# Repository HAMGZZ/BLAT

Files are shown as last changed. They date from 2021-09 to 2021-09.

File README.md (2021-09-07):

# BLAT!
BLAT! is a board that controls the OEM BiModel on the holden commodore SSV series. Initially made to retrofit them to an older 2010 commodore. BLAT! can interface with the [SoundBoi](https://github.com/HAMGZZ/SoundBoi) controller that connects to the car and automatically controls the valves.

## Exhaust Valve Pinout:
1. GND
2. SIGNAL
3. NC
4. +12V
5. NC(May not be present)

## Electronic signal specification
The signal going to the valve must be a 200Hz PWM signal at 10V (0-10V). At 20% duty cycle the valve will be closed and at 80% duty cycle the valve will be open.

BLAT! Converts simple 0-5V logic signal into the required 10v PWM 200Hz signal. Further this board controls the power to the valves through the relay.

## PCB:
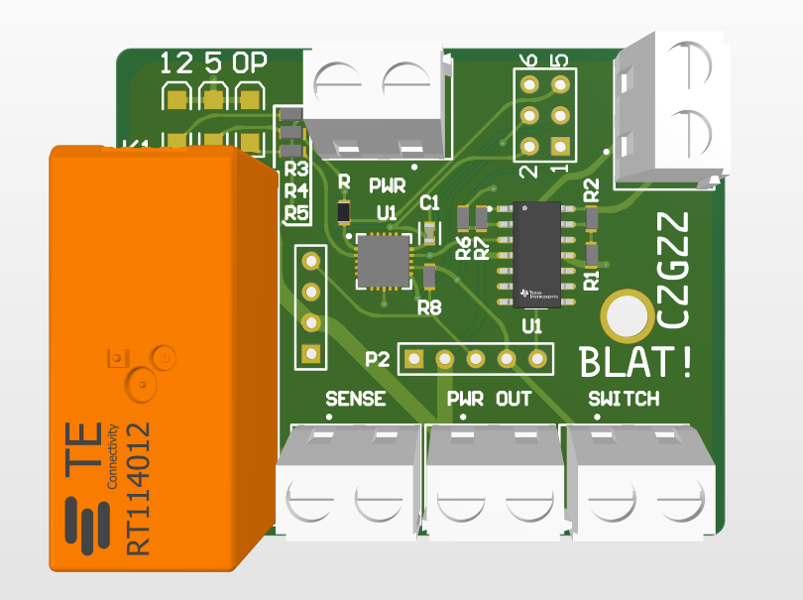
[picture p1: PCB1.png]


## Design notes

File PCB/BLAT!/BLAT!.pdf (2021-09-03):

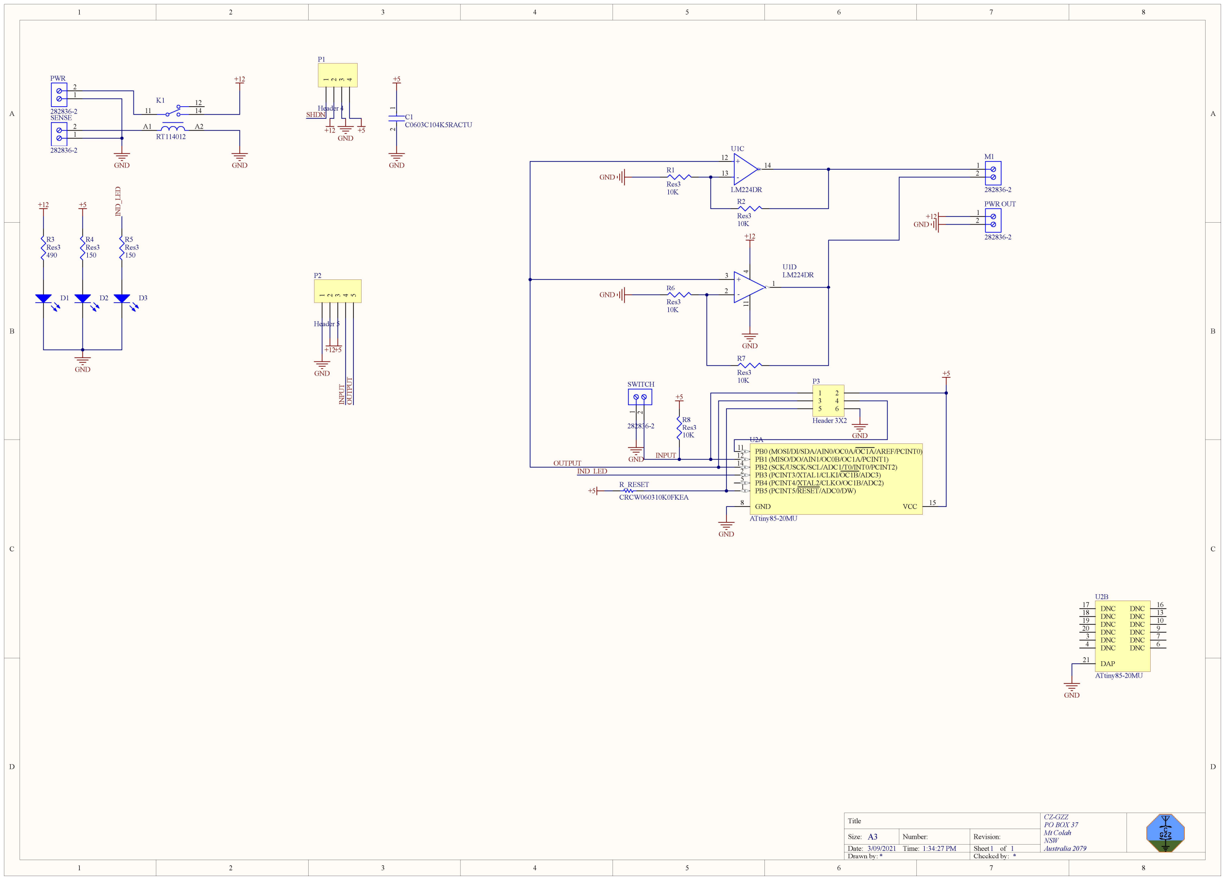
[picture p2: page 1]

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
CZ-GZZ
PO BOX 37
Mt Colah
NSW
3/09/2021 | 1:34:27 PM | 1 | Australia 2079
*

Title

Size: | Number:
Date:
Drawn by:

Revision:
Time: | Sheet | of

A3

Checked by: *

R_RESET
CRCW060310K0FKEA

1 2
C1
C0603C104K5RACTU

GND

GND

GND

1 2
3 4
5 6

P3

Header 3X2

PB5 (PCINT5/RESET/ADC0/DW) 1

PB3 (PCINT3/XTAL1/CLKI/OC1B/ADC3) 2
PB4 (PCINT4/XTAL2/CLKO/OC1B/ADC2) 5

GND 8

PB0 (MOSI/DI/SDA/AIN0/OC0A/OC1A/AREF/PCINT0) 11 PB1 (MISO/DO/AIN1/OC0B/OC1A/PCINT1) 12
PB2 (SCK/USCK/SCL/ADC1/T0/INT0/PCINT2) 14

VCC 15

U2A

ATtiny85-20MU

DNC 17
DNC 18
DNC 19
DNC 20
DNC 3
DNC 4 | DNC | 6
| DNC | 7
DNC | 9
DNC | 10 DNC | 13 DNC | 16

DAP 21

U2B

ATtiny85-20MU

GND

12

13

14 +

U1C

LM224DR

+

3

2

### 1 ⁴ 11

U1D
LM224DR
A1 | A2
| 12
11 14

K1

RT114012

GND

1

2

SENSE

282836-2

1

2

PWR

282836-2

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
Header 4

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
282836-2

10K

R7
Res3

10K

R6
Res3

10K

R2
Res3

10K

R1
Res3

GND

GND

1
2

PWR OUT

282836-2

+12
GND

1
2

SWITCH

282836-2
10K

R8
Res3

+5

GND

D1 | D2 | D3

150

R5
Res3
150

R4
Res3
490

R3
Res3
+12 | +5 | IND_LED

IND_LED

GND | 1
| 2

3

4

5

P2

Header 5

GND

+12+5

+5

INPUT

OUTPUT INPUT OUTPUT

SHDN

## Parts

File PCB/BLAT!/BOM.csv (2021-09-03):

MPN | QTY | PKG | VALUE | COMMENT | DESIGNATOR
LM224DR2G | 1 | SOIC14 |  | 4x OPAMP LM224 | U1
RT114012 | 1 | TH | 12A 12V | 12V Relay | K1
282836-2 | 5 | TH |  | Terminal Block | **
ATTINY85-20MU | 1 | QFN |  | Atmel AVR Microcontroller | U2
RC0603FR-07470RL | 1 | 603 | 470 OHM | 470 OHM Resistor | R3
RC0603FR-07150RL | 2 | 603 | 150 OHM | 150 OHM Resistor | R4 R5
RMCF0603FT10K0CT-ND | 6 | 603 | 10K OHM | 10K OHM Resistor | R1 R2 R6 R7 R8 R
CAPACITOR 1UF | 1 | 603 | 1uF | 1uF Capacitor (UNTESTED) | C1
D24V5F5 | 1 | TH | 5v 500mA | 5v Regulator | N/A
APT3216SYCK | 1 | 1206 |  | Yellow LED | 12
APT3216SURCK | 1 | 1206 |  | Red LED | 5
APT3216CGCK | 1 | 1206 |  | Green LED | OP

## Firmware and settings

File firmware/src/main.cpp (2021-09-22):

/*
 * BLAT! Commodore OEM Bi-model muffler actuator
 * Lewis Hamilton September 2021
 * 
 * Version 1.0.1:
 * - Added pin direction & tuned delay times
 * 
 * Version 1.0.0-alpha:
 * - Initial release
*/

#include <Arduino.h>

#define PWM_OUT 2
#define LED     3
#define STATE   1

#define LONG_TIME       3989    // 4 miliseconds for 80% on or off
#define SHORT_TIME      988     // 1 milisecond for 20% on or off

int main()
{
    long int ton;
    long int toff;
    pinMode(STATE, INPUT_PULLUP);
    pinMode(PWM_OUT, OUTPUT);
    pinMode(LED, OUTPUT);

    while(1)
    {
        if(((digitalRead(STATE))))
        {
            digitalWrite(LED, HIGH);
            ton = LONG_TIME;
            toff = SHORT_TIME;
        }
        else if((!digitalRead(STATE)))
        {
            digitalWrite(LED, LOW);
            ton = SHORT_TIME;
            toff = LONG_TIME;
        }

        digitalWrite(PWM_OUT, HIGH);
        delayMicroseconds(ton);
        digitalWrite(PWM_OUT, LOW);
        delayMicroseconds(toff);

    }
    return 0;
}

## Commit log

2021-09-03 Added PCB & Software
    [BLAT!.PrjPcb, Main.SchDoc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]
2021-09-03 Added more
    [PCB2.PcbDoc]
2021-09-03 Removed junk
    [PCB2.GBL, PCB2.GBO, PCB2.GBP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]
2021-09-03 Added BOM
    [BOM.csv]
2021-09-03 Error in CSV
    [BOM.csv]
2021-09-03 V1.1.0 Added a delay so it dosent change state too fast
    [main.cpp]
2021-09-03 Forgot some parts
    [BOM.csv]
2021-09-07 Added pin directions
